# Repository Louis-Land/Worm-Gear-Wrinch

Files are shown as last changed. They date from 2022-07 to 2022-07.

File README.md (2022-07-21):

# Open Source Worm Gear winch
A public repository to share the stls and Fusion 360 files for a worm gear winch

## My Intent
I am sharing this handy winch because it works well for me and my use case. Hopefully, it works well for someone else. I have been learning Fusion 360 off and on for the last year for smaller projects.

I tried my best to make everything easy to 3d print. I have not noticed an issue with the worm and the plastic shearing on the layer lines. 
I do use heat-set inserts in some locations, which. In most locations, you can use a nut instead.

## Current State

It is powered by a 775 brushed motor and controlled by an Arduino with a motor module that is way overkill because it only draws 1 amp at max load. The remote is another Arduino with an OLED screen powered by a single li-ion battery and type c for changing! The remote can cycle has a cycle function to communicate to multiple winches. 

## What is coming next for this project!
I want to simplify the electronics. I used MOSFETs to control a motor controller. However, I want to switch to a `BTS7960` module or something similar.

It would be neat to shrink the transmitter and offer a single winch version. Currently, the remote can cycle through multiple winches by changing the address.

The spool is not designed the best and needs to be modified to ensure the string cannot jump over and into the side of the winch and is relatively small. 
Its string capacity is about 12 ft. 

I need to design a second winch that does not require the additional off-set pulley.

It would be awesome to add a pulley system to increase pulling power.

## Capacity

I use a micro paracord rope with 100 lbs tests, and I have been able to lift 100 lbs with this winch in its current condition. The winch is comprised of two main parts.

There is the winch which contains the worm gear, and the electric motor that drives the spool. I am using a Worm Gear because it takes zero power to hold stuff in the air and is a relatively small package for the gear ratio.

The second part is the load-bearing pulley. It is designed to handle the forces better when mounted to the ceiling and helps smooth the lifting action.

## What is include

I am sharing the current stls and Fusion 360 files for the winch and transmitter.
I also created a transmitter and receiver for the winch because I wanted a wireless remote to control the winch. 

I will try my best to demonstrate the wiring of the transmitter and receiver and its accompanying Arduino code. It uses 
rf240l+ trans-receviers to communicate with eachother.

I have these winches in my garage to hoist RC planes to the ceiling, and it saves space, and I am too lazy to use a ladder whenever I want to retrieve my planes.

## Assembly

After assembling, you should run it with greased gears to help break everything in for a couple of hours. 

### Printing recommendation:

I believe the smallest print bed you can get away with is 220mm x 220mm

All parts are in the recommended orientation.

5 perimeters
4 top and bottom
31% infill
.2 layer height

Special Printing Instruction for the Worm
5 perimeters
4 top and bottom
31% infill
.12 or .08 layer height

The smaller layer heights help make the power transfer from the worm to the gears much smoother. 
You can get away with a `.2` layer height but not recommended.

NO SUPPORTS NEEDED

Expected Printing time: 
Slow Printers: ~ 48 hrs

Faster Printers: ~ 22 hrs

I am guessing the speed for a slower on an Ender 3. 
I have a Voron V2.4, and it takes about 22 hrs for me to print everything out. 

#### Hardware
Currently, to assemble the winch, you will need the following non-printed parts:

M3 socket head screws:
    60mm * 4-8 for the case
    25mm * 4 for the gear. They act as pins to help reduce the chances of 			searing the plastic layers
    30mm or 35mm for the pin to connect the gear to the rod
    15mm for the spool pin to connect it to the rod
    50mm * 4 for the spools screws. Help it from splitting
    30mm * 4 for the worm mounting bracket

8mm threaded or grounded rod
    could use carbon fiber rods; however, the load capacity is very small but easy to work with

    114MM for the rob that connects the gear and spool
    100-110mm for the rob that connects the worm to the motor
    
    To mark the drill locations for the rod, you will need to assemble it and mark it partially.

8mm to 5mm couplers
https://www.amazon.com/gp/product/B07RMZCLZ3/ref=ppx_yo_dt_b_search_asin_title?ie=UTF8&psc=1

All rotation uses bearings for long service life and increases load capacity
608zz bearings (skateboard)
    Cheap and good: https://www.amazon.com/FaGoBearing-Premium-Inline-Bearings-Roller/dp/B07V3NG2XR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

8mm Thrust bearings
    I am using thrust bearings because the prototype would melt together in certain locations. These eliminate that from happening
    https://www.amazon.com/uxcell-Bearings-Diameter-Thickness-Hardness/dp/B07PDXYQTJ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

Electronics
 775 electric motor
 https://www.amazon.com/775-Motor-12V-6000-12000-Electronic/dp/B08662QSZL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

Arduino Nano: 
https://www.amazon.com/Arduino-Nano-Every-Single-Board/dp/B07VX7MX27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

Seeed Xiao RP2040
https://www.amazon.com/Microcontroller-Dual-Core-MicroPython-CircuitPython-Interfaces/dp/B09NNVNW7M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

Mosfet Module
https://www.amazon.com/Anmbest-High-Power-Adjustment-Electronic-Brightness/dp/B07NWD8W26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

Voltage Step Down Regulator
https://www.amazon.com/MP1584EN-DC-DC-Converter-Adjustable-Module/dp/B01MQGMOKI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

24 voltage power supply
https://www.amazon.com/dp/B07PWZQ4MB/ref=emc_b_5_i

Motor Driver
https://www.amazon.com/gp/product/B075L7YDR9/ref=ppx_yo_dt_b_search_asin_title?ie=UTF8&psc=1

NRF24L0l
https://www.amazon.com/gp/product/B0829ZQ97G/ref=ppx_yo_dt_b_search_asin_title?ie=UTF8&psc=1

### Transmitter Electronics 
Oled Screen
https://www.amazon.com/gp/product/B00O2LKEW2/ref=ppx_yo_dt_b_search_asin_title?ie=UTF8&psc=1

Arduino Nano: 
https://www.amazon.com/Arduino-Nano-Every-Single-Board/dp/B07VX7MX27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

Seeed Xiao RP2040
https://www.amazon.com/Microcontroller-Dual-Core-MicroPython-CircuitPython-Interfaces/dp/B09NNVNW7M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

Momentary Switch
https://www.amazon.com/gp/product/B07QH9WV12/ref=ppx_yo_dt_b_search_asin_title?ie=UTF8&psc=1

5v Step Up Voltage Regulator
https://www.amazon.com/gp/product/B094XJL149/ref=ppx_yo_dt_b_search_asin_title?ie=UTF8&psc=1

1S Li-ion BMS
https://www.amazon.com/gp/product/B07PKND8KG/ref=ppx_yo_dt_b_search_asin_title?ie=UTF8&psc=1

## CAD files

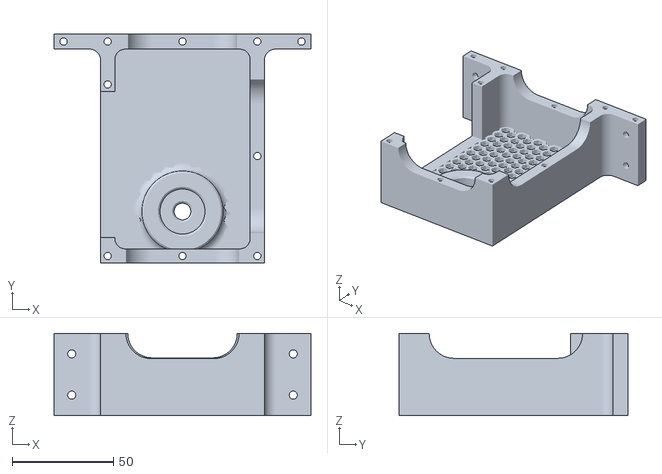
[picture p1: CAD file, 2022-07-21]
Winch/stl/case.stl
126.9 x 113.1 x 40.5

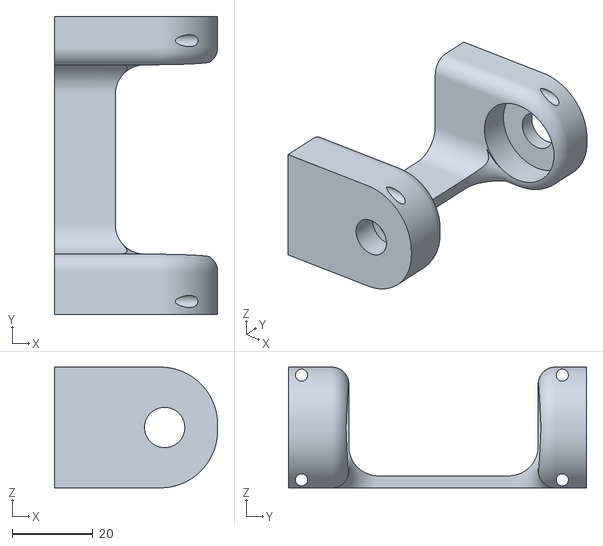
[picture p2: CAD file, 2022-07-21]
Winch/stl/wormMount.stl
40.5 x 74.0 x 30.0

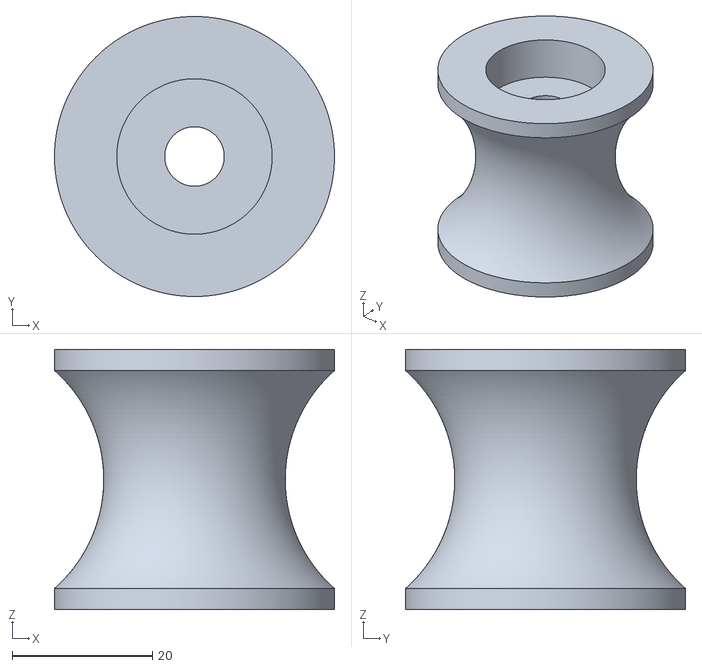
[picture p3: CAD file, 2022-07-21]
Winch/stl/offsetPulley.stl
40.0 x 40.0 x 37.2

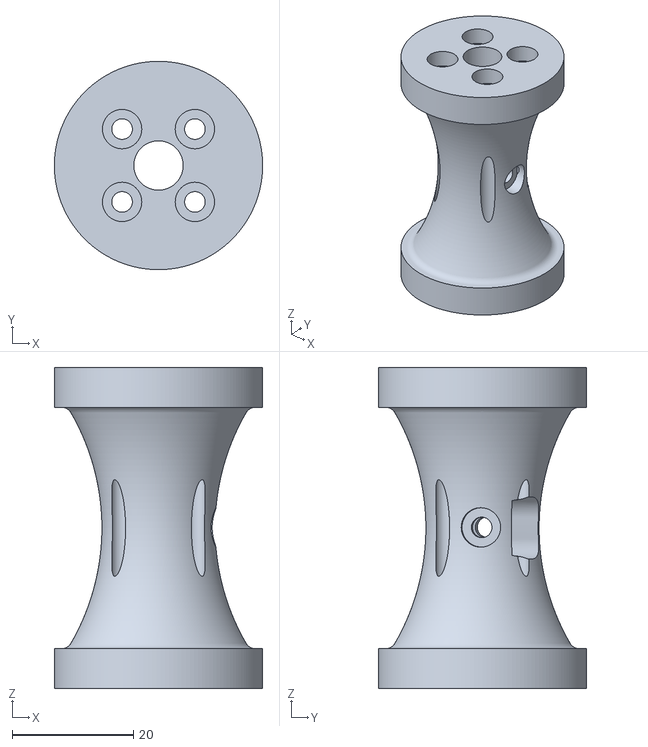
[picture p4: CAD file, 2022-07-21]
Winch/stl/spool.stl
34.4 x 34.4 x 53.0

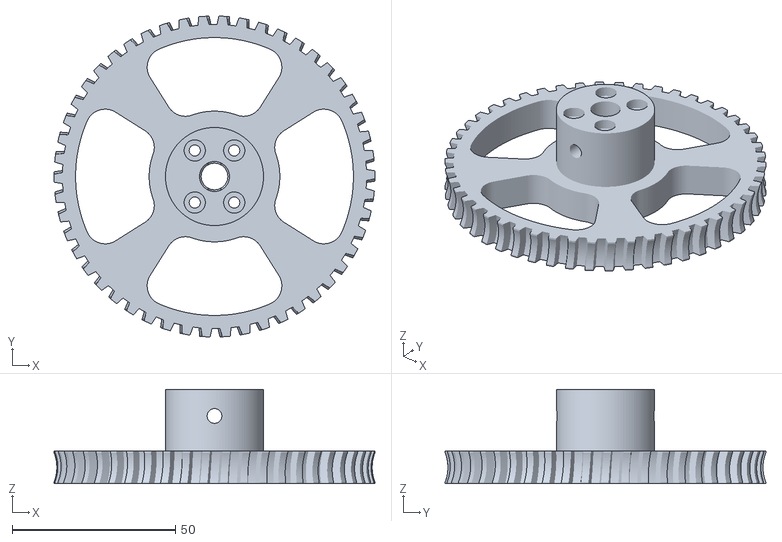
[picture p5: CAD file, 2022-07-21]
Winch/stl/gear.stl
98.2 x 98.2 x 28.9

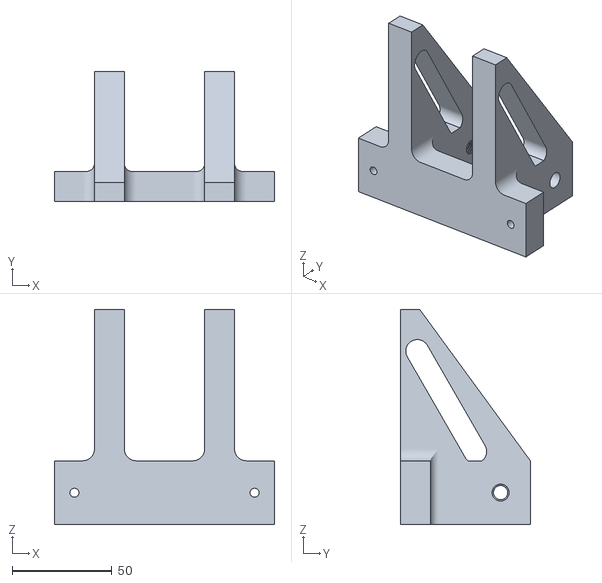
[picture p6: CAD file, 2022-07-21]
Winch/stl/pullyArms.stl
110.2 x 65.0 x 107.9

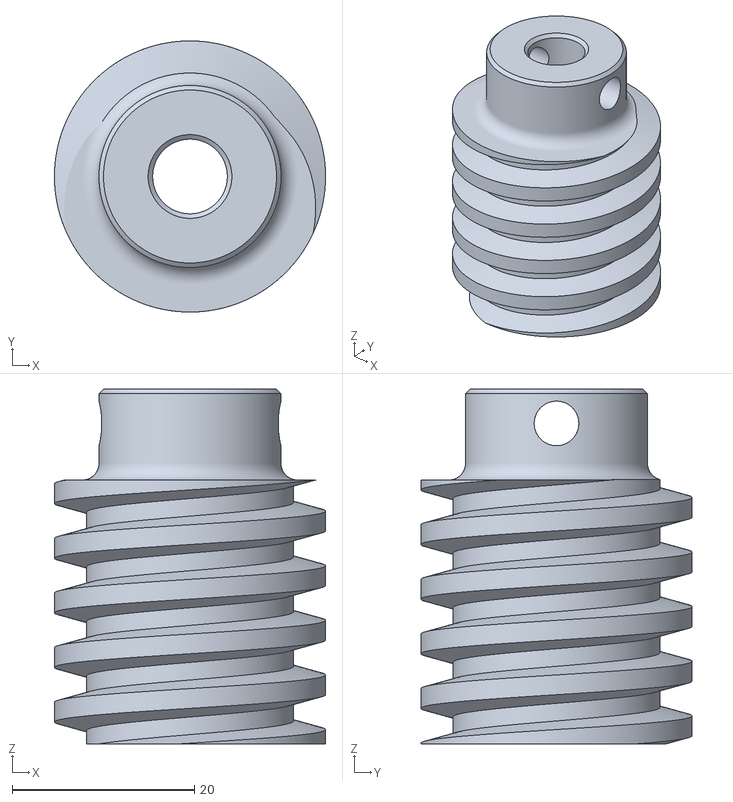
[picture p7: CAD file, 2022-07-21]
Winch/stl/worm.stl
29.8 x 29.8 x 39.0

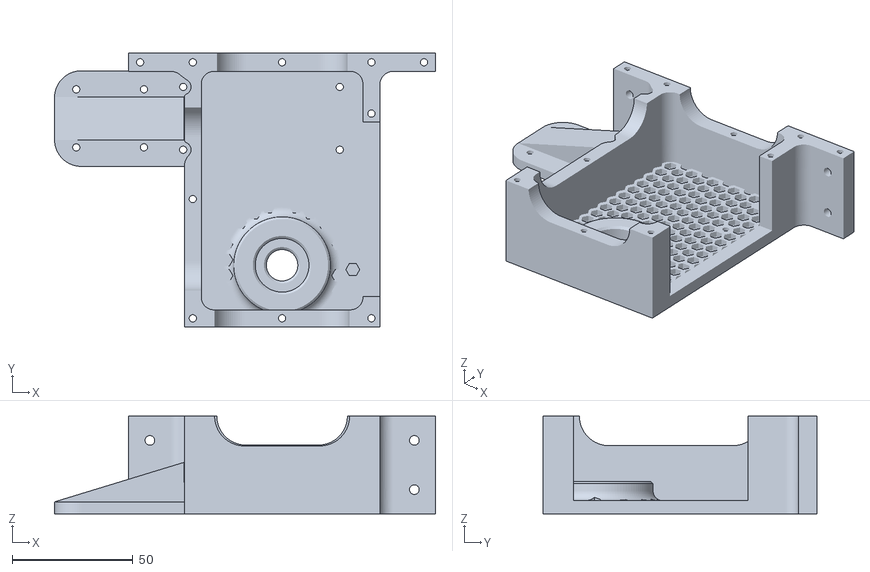
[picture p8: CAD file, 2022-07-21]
Winch/stl/case motor mount.stl
157.6 x 113.1 x 40.5

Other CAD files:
Transmitter/cad/remote v2.f3d

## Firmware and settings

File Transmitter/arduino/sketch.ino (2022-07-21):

// SimpleTxAckPayload - the master or the transmitter

#include <SPI.h>
#include <nRF24L01.h>
#include <RF24.h>

#include <Wire.h>
#include <Adafruit_GFX.h>
#include <Adafruit_SSD1306.h>


#define CE_PIN   9
#define CSN_PIN 10
#define SCREEN_WIDTH 128 // OLED display width, in pixels
#define SCREEN_HEIGHT 64 // OLED display height, in pixels

// Declaration for an SSD1306 display connected to I2C (SDA, SCL pins)
#define OLED_RESET     -1 // Reset pin # (or -1 if sharing Arduino reset pin)
Adafruit_SSD1306 display(SCREEN_WIDTH, SCREEN_HEIGHT, &Wire, OLED_RESET);

int UP_PIN = 8;
int DOWN_PIN = 5;
int CHANNEL_UP = 7;
int CHANNEL_DOWN = 6;

byte slaveAddress[5] = "RxA00";

RF24 radio(CE_PIN, CSN_PIN); // Create a Radio

int txNum = 0;

int ackData[2] = {-1, -1}; // to hold the two values coming from the slave
bool newData = false;

bool sentUp = true;
bool doNothing = true;
bool radioConnected = false;
int currentChannel = 0;
int prevChannel = 0;
int maxChannels = 10;

bool txFailed = false;

unsigned long currentMillis;
unsigned long prevMillis;
unsigned long txIntervalMillis = 20; // send once per second

unsigned long changeChannelPrevMillis;
unsigned long changeChannelInterval = 300; // send once per second


//===============

void setup() {

    Serial.begin(115200);
    pinMode(UP_PIN, INPUT);
    pinMode(DOWN_PIN, INPUT);

    pinMode(CHANNEL_UP, INPUT);
    pinMode(CHANNEL_DOWN, INPUT);

    pinMode(13, OUTPUT);

    if(!display.begin(SSD1306_SWITCHCAPVCC, 0x3C)) { 
        Serial.println(F("SSD1306 allocation failed"));
    }

    display.display();
    display.clearDisplay();

    radio.begin();
    radio.setDataRate( RF24_2MBPS );

    radio.enableAckPayload();

    int powerLeveLBeginning = radio.getPALevel();
    Serial.println("Starting PA Level");
    Serial.println(powerLeveLBeginning);

    radio.enableAckPayload();
    radio.setPALevel( RF24_PA_MIN);
    int powerLevel = radio.getPALevel();
    Serial.println("After Setting PA Level");
    Serial.println(powerLevel);

    if(powerLeveLBeginning != powerLevel && powerLeveLBeginning != 0 && powerLevel == 0) {
        radioConnected = true;
        Serial.println("radio was detected");
    } else {
        Serial.println("radio is not detected");
    }

    // radio.setRetries(1,1); // delay, count
    //                                    
    // 5 gives a 1500 µsec delay which is needed for a 32 byte ackPayload
    radio.openWritingPipe(slaveAddress);
}

//=============

void loop() {

    currentMillis = millis();

    changeChannel();
    masterDisplay();

    if(radioConnected) {
        if (currentMillis - prevMillis >= txIntervalMillis) {
            send();
            prevMillis = millis();
        }
        showData();
    }
}

void masterDisplay() {
    displayRadioStatus();
    displayChannel();
    displayAction();
    display.display();
}

void changeChannel() {

    if (currentMillis - changeChannelPrevMillis >= changeChannelInterval) {
        int up_input = digitalRead(CHANNEL_UP);
        int down_input = digitalRead(CHANNEL_DOWN);

        if(!(up_input == 1 && down_input == 1) && !(up_input == 0 && down_input == 0)) {

            if(up_input) {
                if(currentChannel < maxChannels) {
                    currentChannel++;
                } else {
                    currentChannel = 0;
                }
            } 

            if(down_input) {
                if(currentChannel > 0) {
                    currentChannel--;
                } else {
                    currentChannel = maxChannels;
                } 
            }
        }
        changeChannelPrevMillis = millis();
    }
}

//================

void send() {

    int up_input = digitalRead(UP_PIN);
    int down_input = digitalRead(DOWN_PIN);

    if(!(up_input == 1 && down_input == 1) && !(up_input == 0 && down_input == 0)) {
        doNothing = false;
        if(up_input == 1) {
            sentUp = true;
        }

        if(down_input == 1) {
            sentUp = false;
        } 
    } else {
        doNothing = true;
    }

    sendData();
 }

 void settingPipe() {
    String temp;
    if(currentChannel >= 10) {
        temp = "RxA"+ String(currentChannel);
    } else {
        temp = "RxA0"+ String(currentChannel);
    }
    temp.getBytes(slaveAddress, 7);
    radio.openWritingPipe(slaveAddress);
 }


//=================

void sendData() {
             
    settingPipe();
    char command [20] = "Command";
    bool rslt;

    if(doNothing == true) {
        strcat((char*)command, " NOTHING");
        rslt = radio.write(&command, sizeof(command));
        Serial.print(command );
    } else {
        if(sentUp) {
            strcat((char*)command, " UP");
            rslt = radio.write( &command , sizeof(command));
            Serial.print(command );
        } else {
            strcat((char*)command, " DOWN");
            rslt = radio.write( &command, sizeof(command));
            Serial.print(command);
        }
    }

    // Always use sizeof() as it gives the size as the number of bytes.
    // For example if dataToSend was an int sizeof() would correctly return 2
    if (rslt) {
        if ( radio.isAckPayloadAvailable() ) {
            txFailed = false;
            radio.read(&ackData, sizeof(ackData));
            newData = true;
        } else {
            txFailed = false;
            Serial.println("  Acknowledge but no data ");
        }
    } else {
        txFailed = true;
        Serial.println("  Tx failed");
    }
}

void showData() {
    if (newData == true) {
        Serial.print("  Acknowledge data ");
        Serial.print(ackData[0]);
        Serial.print(", ");
        Serial.println(ackData[1]);
        Serial.println();
        newData = false;
    }
}

//================

void updateMessage() {
    // so you can see that new data is being sent
    txNum += 1;
    if (sentUp) {
        txNum = '0';
        sentUp = false;
    } else {
        txNum = 'P';
        sentUp = true;
    }

    // dataToSend[8] = txNum;
}

void displayRadioStatus(void) {

    String text = "Disconnected";
    // Not all the characters will fit on the display. This is normal.
    // Library will draw what it can and the rest will be clipped.
    if(radioConnected) {
    text = "Connected     RX: ";
    }

    print(text, 0, 0);

    String connected = String(!txFailed);

    overridePrint(connected);
}

void displayChannel(void) {
    print("Channel ", 0, 20);
    String temp = String((char *)slaveAddress);
    overridePrint(String(currentChannel) + " " + temp + "   ");
}

void displayAction(void) {
    String informationalText = "    ";

    print("Action ", 0, 40);  
    display.setTextColor(WHITE, BLACK);
    
    if(!doNothing) {
        if(sentUp) {
            informationalText = "UP  ";
        } else {
            informationalText = "DOWN";
        }
    }

    overridePrint(informationalText);
}

// void println(String text, int x, int y) {
//     setBasicTextSettings();
//     display.println(text);
// }

void print(String text, int x, int y) {
    setBasicTextSettings(x, y);
    display.print(text);
}

void overridePrint(String text) {
    display.setTextColor(WHITE, BLACK);
    display.print(text);
}

void setBasicTextSettings(int x, int y) {
    display.setTextSize(1);      // Normal 1:1 pixel scale
    display.setTextColor(WHITE); // Draw white text
    display.setCursor(x, y);     // Start at top-left corner
    display.cp437(true);         // Use full 256 char 'Code Page 437' font
}

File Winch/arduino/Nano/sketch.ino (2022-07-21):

// SimpleRxAckPayload- the slave or the receiver

#include <SPI.h>
#include <nRF24L01.h>
#include <RF24.h>

#define CE_PIN   9
#define CSN_PIN 10

const byte thisSlaveAddress[6] = "RxA03";

RF24 radio(CE_PIN, CSN_PIN);

int downPin = 8;
int upPin = 7;
int enabledPin = 6;

char dataReceived[20]; // this must match dataToSend in the TX
int ackData[2] = {109, -4000}; // the two values to be sent to the master
bool newData = false;
int idleTime = 0;
bool commandForMe = false;

//==============

void setup() {

    Serial.begin(115200);

    Serial.println("SimpleRxAckPayload Starting");
    radio.begin();
    radio.setDataRate( RF24_2MBPS );
    radio.openReadingPipe(1, thisSlaveAddress);

    int powerLeveLBeginning = radio.getPALevel();
    Serial.println("Starting PA Level");
    Serial.println(powerLeveLBeginning);

    radio.enableAckPayload();
    radio.setPALevel( RF24_PA_MIN );
    int powerLevel = radio.getPALevel();
    Serial.println("After Setting PA Level");
    Serial.println(powerLevel);

    if(powerLeveLBeginning != powerLevel) {
        Serial.println("radio was detected");
    } else {
        Serial.println("radio is not detected");
    }

    radio.startListening();

    radio.writeAckPayload(1, &ackData, sizeof(ackData)); // pre-load data

    pinMode(upPin, OUTPUT);
    pinMode(downPin, OUTPUT);

    digitalWrite(upPin, LOW);
    digitalWrite(downPin, LOW);
}

//==========

void loop() {
    getData();
    showData();
}

//============

void getData() {
    if ( radio.available() ) {
        radio.read( &dataReceived, sizeof(dataReceived) );
        updateReplyData();
        newData = true;
    }
}

//================

void showData() {

    if(idleTime > 10005) {
        digitalWrite(enabledPin, LOW);
        digitalWrite(downPin, LOW);
        digitalWrite(upPin, LOW);
    }

    if (newData == true) {
        idleTime = 0;
        char upCommandText[20] = "Command UP";
        char downCommandText[20] = "Command DOWN";
        char nothingCommand[20] = "Command NOTHING";

        bool nothingComparsion = strcmp(dataReceived, nothingCommand) == 0;

        bool emptyComparsion = strcmp(dataReceived, "") == 0;

        if(!emptyComparsion) {
            if(strcmp(dataReceived, upCommandText) == 0 && !nothingComparsion) {
                Serial.println("GOING UP");
                digitalWrite(downPin, HIGH);
                digitalWrite(upPin, LOW);
            } else if(strcmp(dataReceived, downCommandText) == 0 && !nothingComparsion) {
                Serial.println("GOING DOWN");
                digitalWrite(upPin, HIGH);
                digitalWrite(downPin, LOW);
            } else if(nothingComparsion) {
                Serial.println("NOTHING");
                digitalWrite(downPin, LOW);
                digitalWrite(upPin, LOW);
                digitalWrite(enabledPin, HIGH);
            }
        } 
        newData = false;
    } else {
        idleTime++;
    }

}

//================

void updateReplyData() {
    ackData[0] -= 1;
    ackData[1] -= 1;
    if (ackData[0] < 100) {
        ackData[0] = 109;
    }
    if (ackData[1] < -4009) {
        ackData[1] = -4000;
    }
    radio.writeAckPayload(1, &ackData, sizeof(ackData)); // load the payload for the next time
}
